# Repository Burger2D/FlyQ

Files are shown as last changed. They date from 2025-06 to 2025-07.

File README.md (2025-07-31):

# FlyQ
An Ultralight fixed-wing autonomous UAV. It is designed to be a flying wing with a single pusher propeller at the back. The airframe is made of XPS foamboard for lightweight-ness.
I plan to eventually fly it with a sidestick.

Why?
It all started with [this video by rctestflight](https://www.youtube.com/watch?v=ULlNktaOUy8), I think. I was fascinated by the idea of a fixed-wing flying objects that and the pictures it captured. I wanted to build something like that, but I wanted it to be ultralight and autonomous. So I started researching on the different types of drones and decided what I want to build. I wanted to start a YSWS with this too (#firefly plug) that is basically this. I am happy I am able to get this far with it.

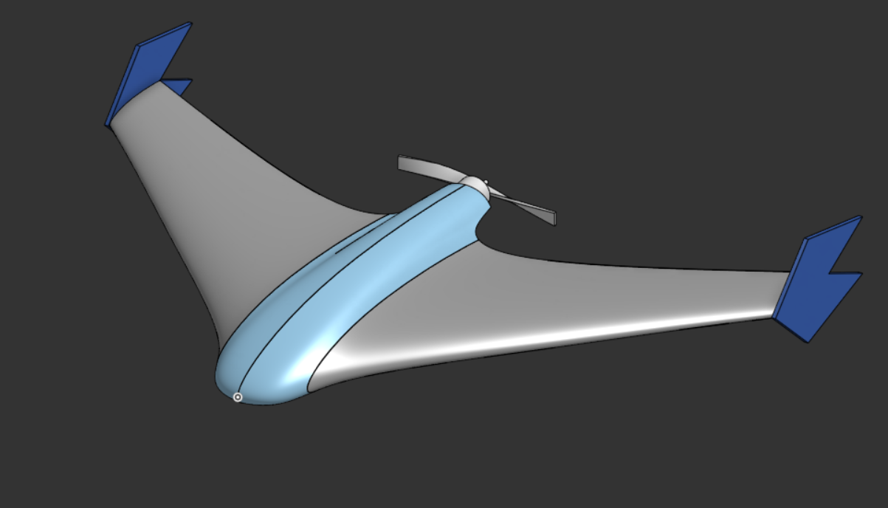
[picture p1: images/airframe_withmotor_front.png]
FlyQ Airframe Design Front

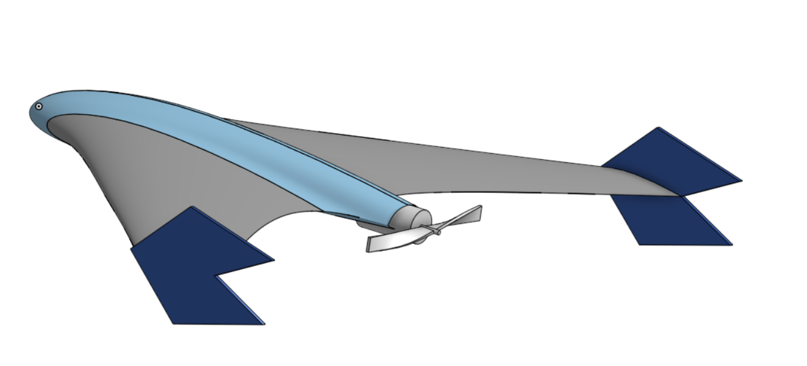
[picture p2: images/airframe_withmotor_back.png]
FlyQ Airframe Design Back

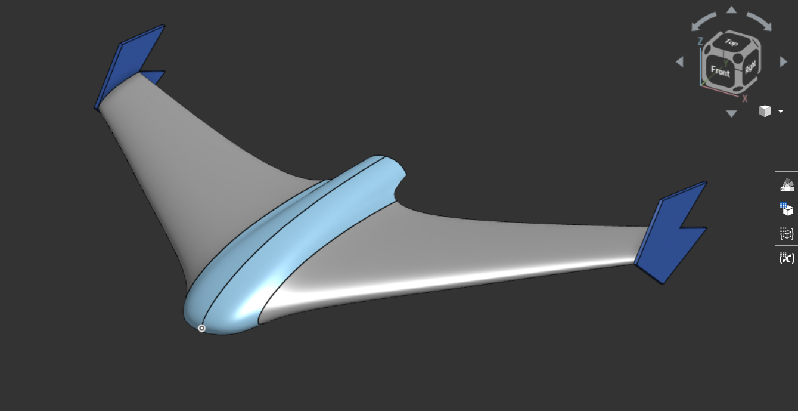
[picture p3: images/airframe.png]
FlyQ Airframe Design CAD


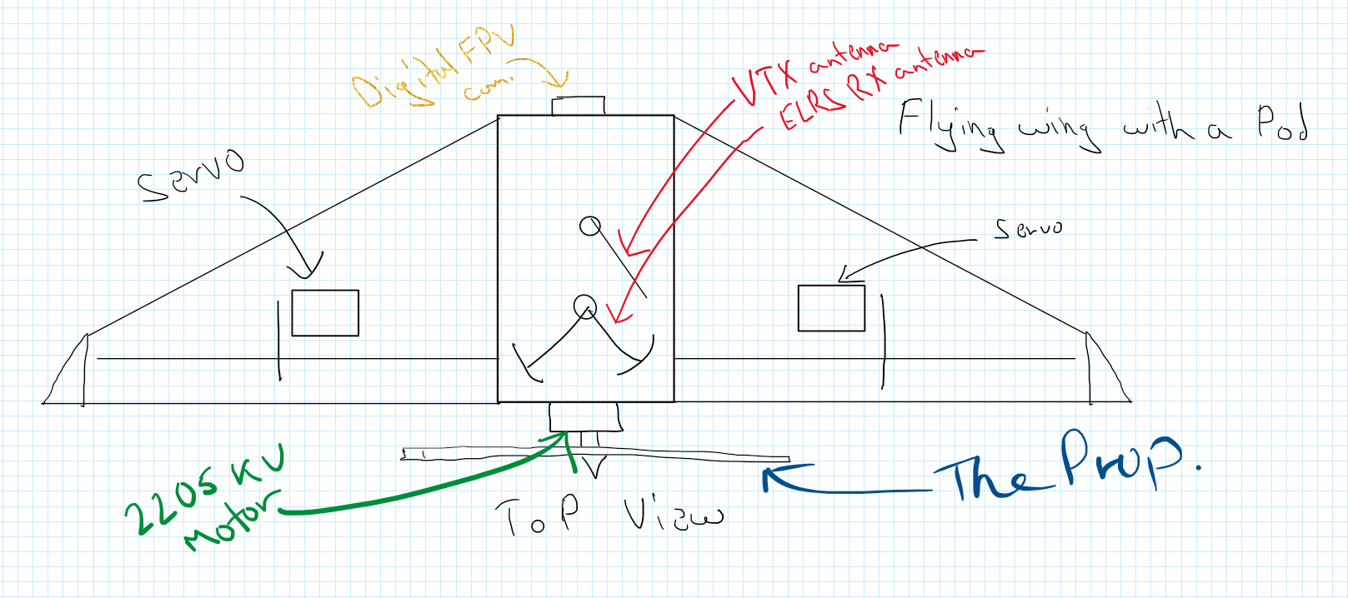
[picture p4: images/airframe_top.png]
FlyQ Airframe Design Top


List:
- [x] Finalise Project Goals
- [x] Finalised Parts List
- [x] Finalised Budget
- [x] Finalised Design
- [x] Tech Work, Arch.

## BOM

| Category | Component Name | Part Number | Quantity | Unit Cost | Total Cost | Supplier | Link |
| --- | --- | --- | --- | --- | --- | --- | --- |
| FC | SpeedyBee F405 WING MINI Fixed Wing Flight Controller | 2008125 | 1 | $38.54 | $38.54 | Speedybee via Banggoods | [https://www.banggood.com/SpeedyBee-F405-WING-MINI-Fixed-Wing-Flight-Controller-Support-INAV-Ardupilot-VTOL-for-RC-Airplane-p-2008125.html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](https://www.banggood.com/SpeedyBee-F405-WING-MINI-Fixed-Wing-Flight-Controller-Support-INAV-Ardupilot-VTOL-for-RC-Airplane-p-2008125.html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) |
| GPS | HGLRC M100 5883 GPS Module M10 Chip with QMC 5883 Compass Ceramic Antenna | 1993147 | 1 | $13.95 | $13.95 | HGLRC via Banggoods | [https://www.banggood.com/HGLRC-M100-5883-GPS-Module-M10-Chip-with-QMC-5883-Compass-Ceramic-Antenna-for-RC-Drone-FPV-Racing-Helicopter-Airplane-p-1993147.html?ID=5222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](https://www.banggood.com/HGLRC-M100-5883-GPS-Module-M10-Chip-with-QMC-5883-Compass-Ceramic-Antenna-for-RC-Drone-FPV-Racing-Helicopter-Airplane-p-1993147.html?ID=5222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) |
| Motor | Readytosky 2205 2300KV 3-4S CW CCW Brushless Motor | 447-M-020 | 2 | $8.66 | $8.66 | Readytosky via Evelta | [https://evelta.com/readytosky-2205-2300kv-3-4s-cw-ccw-brushless-motor/?](https://evelta.com/readytosky-2205-2300kv-3-4s-cw-ccw-brushless-motor/?) |
| ESC | Readytosky 30A 2-4S ESC with 3.5mm Banana Connector | 447-E-064-B21 | 1 | $5.51 | $5.51 | Readytosky via Evelta | [https://evelta.com/readytosky-30a-2-4s-esc-with-3-5mm-banana-connector/](https://evelta.com/readytosky-30a-2-4s-esc-with-3-5mm-banana-connector/) |
| ELRS RX | Radiomaster RP3 ExpressLRS ELRS 2.4GHz LNA+PA Dual Antenna Nano Diversity Receiver | 1978249 | 1 | $19.95 | $19.95 | Radiomaster via Banggoods | [https://www.banggood.com/Radiomaster-RP3-ExpressLRS-ELRS-2_4GHz-LNA+PA-Dual-Antenna-Nano-Diversity-Receiver-for-Whoops-FPV-RC-Racing-Drone-Airplane-p-1978249.html](https://www.banggood.com/Radiomaster-RP3-ExpressLRS-ELRS-2_4GHz-LNA+PA-Dual-Antenna-Nano-Diversity-Receiver-for-Whoops-FPV-RC-Racing-Drone-Airplane-p-1978249.html) |
| Battery Charger | TooklitRC M6D Charger | 2025007 | 1 | $40.00 | $40.00 | TookkitRC via Amazon | [https://www.banggood.com/Eachine-Sphere-Link-5_8GHz-WIFI-Digital-HD-800mW-FPV-Transmitter-VTX-with-1080P-FOV-140-FPV-Camera-MAVLINK-Protocol-Based-on-OpenIPC-for-RC-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](https://www.amazon.in/ToolkitRC-Screen-Multi-Function-Charger-Diagnostics/dp/B07W2X7L6D) |
| Prop | Pro-Range Propellers 6042(6X4.2) Tri Blade Flash 2CW+2CCW 2 Pair Pack- Black | | 1 | $2.97 | $2.97 | Pro-range via Robu.in | [https://robu.in/product/orange-hd-604260x4-2-tri-blade-flash-propellers-2cw2ccw-2-pair-black/](https://robu.in/product/orange-hd-604260x4-2-tri-blade-flash-propellers-2cw2ccw-2-pair-black/) |
| Battery | Samsung INR18650-35E 7.4V 3500mAh 2C 2S1P Li-ion Battery Pack | | 1 | $12.00 | $12.00 | Pro-range via Robu.in | [https://robu.in/product/samsung-inr18650-35e-7-4v-3500mah-2c-2s1p-li-ion-battery-pack/](https://robu.in/product/samsung-inr18650-35e-7-4v-3500mah-2c-2s1p-li-ion-battery-pack/) |
| Drone Airframe | LW-PLA | | 1 | $35 | $35 | Generic via Amazon |  [https://3dzone.in/polymaker-polylite-lw-pla-filament-1-75-0-8kg/?attribute_pa_color=black](https://3dzone.in/polymaker-polylite-lw-pla-filament-1-75-0-8kg/?attribute_pa_color=black) |
| Drone Airframe | Carbon Fiber Spars | | 1 | $3.22 | $3.22 | Generic via Robu.in | [https://robu.in/product/pultruded-carbon-fiber-tube-hollow-3mmod-1-5mm-id-1000mm-pack-of-2](https://robu.in/product/pultruded-carbon-fiber-tube-hollow-3mmod-1-5mm-id-1000mm-pack-of-2) |
| Misc. | Misc. | | | $15.00 | $15.00 | | |
| Price Increases. | Misc. | | | $35.00-40.00 | $35-40.00 | | |
| | Total | | | | ~$250 | | |
> Price Increases in the above table refer to the increase in price due to a sale ending in Banggoods (Hobby days), from where I am sourcing some parts, this is to offset that cost. 
> Misc. refers to other stuff I may need during the build, Plastic Glue, shipping costs to mohid to ship a few things etc. 

Onshape: https://cad.onshape.com/documents/3a31bd101055f48e2c57a97f/w/3223f853520e071ef3d94c1a/e/74b33148177611be13b0c74b

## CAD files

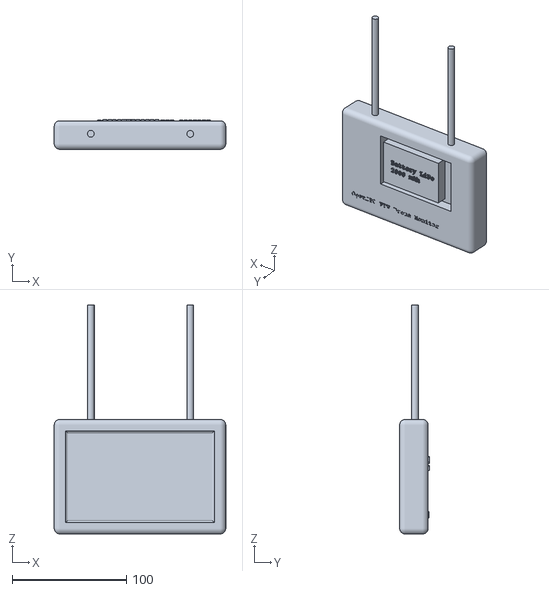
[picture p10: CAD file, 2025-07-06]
FPV_monitor.stl
150.0 x 26.0 x 200.2

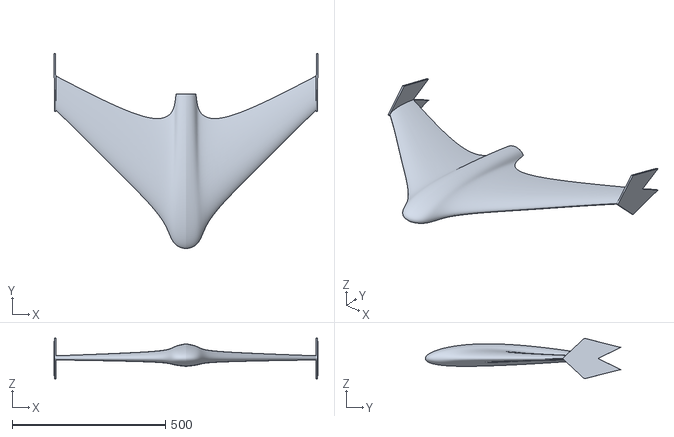
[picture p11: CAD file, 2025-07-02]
airframe_onshape.stl
861.5 x 637.1 x 132.3

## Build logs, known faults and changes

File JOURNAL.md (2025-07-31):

---
title: "FlyQ"
author: "Burger"
description: "Fixed-wing ultralight autonomous UAV"
created_at: "2025-06-01"
total_time: "~50 hours"

---

# FlyQ
An Ultralight fixed wing autonomous UAV.
Note: Not all parts listed from June 1st-6th are used.

## June 1st
Project inception, I researched on the different types of drones and decided what I want to build. Here is all of the research condensed down for reader's consumption.
Project goals:
 - ultralight
 - should have autonomous flying capabilities with failsafe RTH
 - medium range (4-8 km)
 - cameras
 - fixed wing
 - durable
 
Considering all goals, I have decided:
It is going to be a flying wing design with single rotor at the back (pusher).

FlyQ Airframe Design Top

Time spent: ~3-4 hrs (research)

## June 2nd
Agenda: Airframe
I am researching on the airframe, how it's going to be made, design desisions, extra provisions etc.
I have decided it is best to buy a commercial frame for it being made out of molded EPP foam goes a long way towards crash resistance (EPP foam compresses and does not break (shatter) like defron sheets if I were to DIY it). There are a few downsides to this, notablily this kinda makes future customization on the drone itself a bit difficult but I think that is acctable considering the other factors.
Time spent: ~2-3 hrs
I had some more time today so I have decided to look into which commercial frame that is readyly available here that can be bought.
I am going for a single prop design as it is cheaper due to only one motor being persent and the cruise current being lower for the same reason.
I've chosen the 'Reptile S800 V2 Flying Wing'

I chose this due to it's avaibility in an Indian store and alignment with the project goals. It's made with EPP ensuring the drone dosen't break on impact.
Time spent: ~3 hrs

## June 3rd
Agenda: Flight Control systems
I'll try to decide which control systems to put on drone as per my budget and other factors like compatibility with Ardupilot/INAV (autonomy), ELRS etc.
I've decided to go with the "SpeedyBee F405 WING MINI Fixed Wing Flight Controller"


It is very light at 23g and supports INAV and Ardupilot. It is well within budget at US$35.99 (around $47 USD in Indian sites)
I've checked out some 40 FCs but this seems to be the best in it's capabilities and price based on the STM32F405. It has integrated IMU, barometer and OSD.

I've read the INAV and Ardupilot docs to compare which one would be simpler for my use case. As I see, Ardupilot is a much more sophisticated solution for drone piloting, while [INAV](https://github.com/iNavFlight/inav) is simpler, and fits my usecase better, which is autonomy for some time, not very long range ops.

In my search for a good FC, I initially came across Matek F405-Wing, which is a nice FC and what I was going to use until I continued searching and found the SpeedyBee F405 Wing Mini, which is much lighter than the Matek version. I also came across the Matek F722-Wing, it is also a nice FC, a little too nice, it's too expensive for this lightweight platform. Betaflight FCs (F411s etc) were too slow to support everything and that kinda raised some questions about it's stabilty running everything.
This FC was a stack option containing PDBs and current sensors inbuilt. Also has Barometers for altitude measurement. 
My search for the FC was narrowed down with the help of INAV docs with which I could tell if it had the minimum requirements for my needs, as it needed to run INAV. (ref feature 1 [here](https://github.com/iNavFlight/inav?tab=readme-ov-file#features))
Read some more about flying with INAV here [https://github.com/iNavFlight/inav/blob/master/docs/INAV_Fixed_Wing_Setup_Guide.pdf](https://github.com/iNavFlight/inav/blob/master/docs/INAV_Fixed_Wing_Setup_Guide.pdf) and [https://github.com/iNavFlight/inav/blob/master/docs/Navigation.md](https://github.com/iNavFlight/inav/blob/master/docs/Navigation.md)

Also selected the GPS module to be used with this FC, it's a Flywoo GOKU GM10 Mini V3 GPS

Time spent: ~4 hrs

## June 4th
Agenda: Other parts
Selecting other parts in accordance with compatibilty with FC, budget and project goals.
### Motor
XING 2205 FPV Motor (12/M2) - 2300KV

Within budget, efficient rating.
This is a popular FPV motor within FPV circles. At 2300KV, it produces enough thrust to cruise comfortably with just the right amount of energy. It's reliable, lightweight and efficient, ideal for this project.
### ESC
Readytosky 40A 2-6S Multi-Rotor UAV Drone ESC
Readytosky 40A 2-6S Multi-Rotor UAV Drone ESC, Brushless Electronic Speed Controller for F450, X500, S500, ZD550 RC Helicopters and Quadcopters, OPTO Design, Lightweight 33.2g.
Also, within budget and has a sufficient rating.
At 40A, this is more than enough for what the motor will ever experience, with enough headroom for boosts past the normal every once in a while. It is reasonably priced and well-known.
### ELRS RX

MATEKSYS ELRS 2.4GHz Vario Receiver ELRS-R24-V
This is an important component (although one could say this for all of them). It's an [ELRS](https://www.expresslrs.org/) receiver, which stands for [Express Long Range System](https://www.expresslrs.org/), is a "High Performance Open Source Radio Control Link" optimised for long range and low latency. Read a lot in the [ELRS docs](https://www.expresslrs.org/software/mavlink/). It can pull some long-range (50+ km) stuff even on 2.4 GHz.

### Camera DVR

It is a RunCam Mini FPV DVR, fits right in the budget. 
It was meh, i didn't quite like it as it can't record in HD but I guess for that price it's the best I can get.

### Camera
Buy Caddx Ant Lite Analog Camera at Best Price
It's a Caddx Ant Lite Analog Camera (FPV Cycle Edition) (4:3), cheapest while having great quality.
Its cheap, at this price point it's hard to beat. Great for this build.
This is cool, cheap and probably not the camera for drones so would need to hack it for it to work with the FC and VTx.

Spent a lot of time reading the ELRS and INAV docs. Also got help from the Oscar Liang blog. Spent some time researching batteries.

Time spent: ~6-8 hrs

## June 5th
Remaining electronic stuff for the drone.

### VTX
 SpeedyBee TX800 5.8 GHz VTX
 One of the few available VTxs here, it's cheap-er than most and the transmit power is under limits and enough for mid range stuff.
### Battery

 Samsung INR18650-35E 7.4V 3500mAh 2C 2S1P Li-ion Battery Pack
 Nice value for the battery pack, it's good that it's made by robu and sold by robu.
### VTX Antenna
Buy Pagoda 2 Antenna 5.8GHz with cover Online at Best Price in India
Pagoda 2 Antenna 5.8GHz with cover
Good antenna, cheap, would be used for the drone VTx.

Time spent: ~4-5 hrs

## June 6th
Ground station stuff

### VRX
5.8G UVC OTG Android AV Phone Receiver
5.8G UVC OTG Android AV Phone Receiver

> ## Budget check (retail prices at 1USD = 85.76INR)
>  Airframe - $49.05
>  FC - $39.77
>  GPS - $19.80
>  Motor - $9.32
>  ESC (!!) - $8.71
>  ELRS RX - $29.71
>  DVR - $17.99
>  Camera - $18.80
>  VTX - $28 USD 
>  Battery - $12.57
>  Antenna (drone) - $4.19
>  ### Total till now - $ 246.94
Prices taken from the best retailers found. That took too long. Finding the cheapest non-scammy retailer for niche stuff is a bit hard. More so in India, thankfully, I was able to find retailers for all the parts. 

Ah, Houston, we have a problem.
That price is too high; it's more than I thought for just this part of the project. I must do something about it. I suppose I'd have to allow myself to import and change parts for better, more cost-effective alternatives. 

Did some research on drone parts from YouTube and Oscar Liang's blog. They are a nice resource on builds like these, not just these but most other builds would benifit from the infomative blogs and youtube reviews.
Time spent: 4.5 hrs

## Break
I took a break. Returned on June 15th

We can do better. Revamping materials and stategry to bring this greatly under budget.
### To do so, we're changing the following:
- Allowing imports
- Frame
- FC
- Camera and VTX

I lost of count of time spent on doing this, I have been at it for 2+ days at this point.

But I have selected all the new parts.

> I've listed the new parts below, the cateories that aren't listed have kept their initial selection.
> GPS - HGLRC M100 5883 GPS Module M10 Chip with QMC 5883 Compass Ceramic Antenna - $14.39
> Motor - Readytosky 2205 2300KV 3-4S CW CCW Brushless Motor -  $8.69
> ESC - Generic ESC 30A - $4
> ELRS RX - Radiomaster RP3 ExpressLRS ELRS 2.4GHz LNA+PA Dual Antenna Nano Diversity Receiver for Whoops FPV RC Racing Drone Airplane - $21.73
> FPV setup, full (VTX, VRX, Camera, Antenna Combo) - Eachine Sphere Link 5.8GHz WIFI Digital HD 800mW - $67.35
> Servo - TowerPro SG90 9G Mini - $4

This brings the drone hardware cost below $170 (from ~$250)

Below is the design for the drone airframe, it's going to be built out of XPS foam boards, supported by carbon fiber spars and reinforced with packing tape.

FlyQ Airframe Design Top
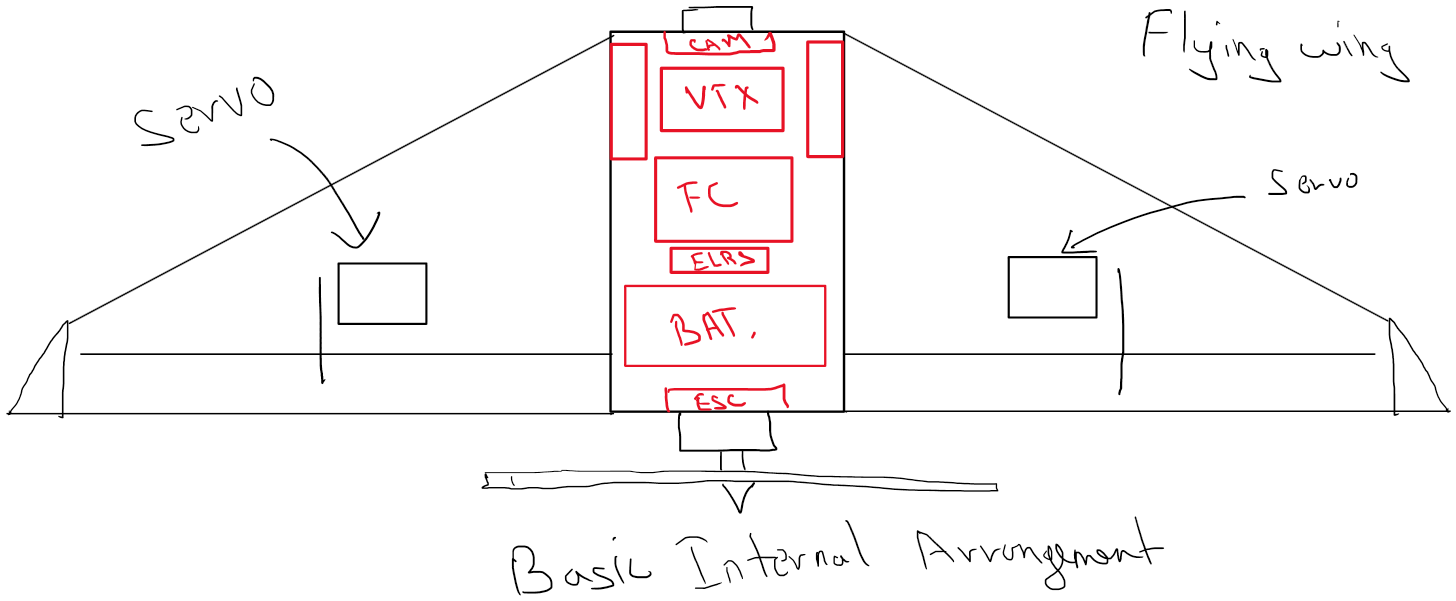
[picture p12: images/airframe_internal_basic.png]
FlyQ Airframe Design Inside (basic)


For Accurate wiring, I'd need to have the hardware in hand, so I will not be able to do that until the parts arrive.

For firmware, I'd be using INAV 6.0 for autonomy and Rocketmaster Pocket for ELRS control link, and using it will passthrough telementry data to the ground station.

I am also designing a custom PCB DVR for the drone, it will be used to record the video feed from the camera on the drone onto a SD card onboard for even higher image quality and data recovery.

For FPV setup, I will be using the Eachine Sphere Link 5.8GHz WIFI Digital HD 800mW, which is a combo of VTX, VRX, Camera and Antenna. It is a digital setup and will provide much better image quality than analog setups, at a cost that is cheaper than most.

For the FPV ground viewing, I'd be using a phone initially with plans to bind it with a rpi02w soon.

I have carefully selected all the parts to ensure they are compatible with each other and fit within the budget. I have also taken into account the weight of each component to ensure the drone remains ultralight.

XPS foam boards are great for this project as they are lightweight and help me keep the drone within limits.

This concludes Part 1 of the FlyQ project.

spent ~15 days designing, refining and finalizing the design, parts and budget.

## 27th June
wait a second, wasn't that the end?
apparently not, there's more to come.

Designed with a meticulous selection of components to achieve a compact, efficient, and high-performance system.

I present you FlyQ, the ultralight fixed-wing autonomous UAV.

FlyQ Airframe Design Top
.stl files in root

# Summery:

Bit of a rewrite, but this improves the formatting of the initial part (sourcing parts [new ones])

Let us recap the project goals
Project goals:
 - ultralight
 - should have autonomous flying capabilities with failsafe RTH
 - medium range (4-8 km)
 - cameras
 - fixed wing
 - durable

|Sr. No.|Image |Name |Category |Sub-Category|Main Use |Considerations while choosing |Cost  |Extra remarks |
|---|---|---|---|---|---|---|---|---|
|1 |https://cdn11.bigcommerce.com/s-fhxxhuiq8q/images/stencil/500x500/products/240/1367/SB_WING-MINI-1__04828.1707096339.jpg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|SpeedyBee F405 WING MINI Fixed Wing Flight Controller |Electronics|Main control|Flight Controller|Cheap, Very light, Support INAV/Ardupilot, built in barometer, current sensor, OSD and UART capabilities, ecosystem. Entire stack|$39.00|Will probably buy from Banggoods as while it's $2 cheaper when directly compared, the shipping cost takes ~$15.|
|2 |https://m.media-amazon.com/images/I/51ASMWWGR7L._UF1000,1000_QL80_.jpg |HGLRC M100 5883 GPS Module M10 Chip with QMC 5883 Compass Ceramic Antenna |Electronics|Main control|GPS |Cheap, Has Compass, Accuracy, Latest M10 chip, Has a compass, Lightweight |$13.00| |
|3 |https://m.media-amazon.com/images/I/41W5V3w09pL._UF350,350_QL80_.jpg |Readytosky 2205 2300KV 3-4S CW CCW Brushless Motor |Electronics|Main control|Motor |Well known FPV motor, reletively lightweight |$8.69 |India shop |
|4 |https://ae01.alicdn.com/kf/Sd7f9c6000a61405a96563ed8aa87b3907.jpg_960x960.jpg |Readytosky 40A 2-4S ESC with 3.5mm Banana Connector |Electronics|Power |ESC |Well known FPV ESC, within limits, reletively lightweight and cheap |$6.14 |would have bought the 30A 2-4S varient for a dollar less if it was in stock; Have to solder connections |
|5 |https://ueeshop.ly200-cdn.com/u_file/UPAX/UPAX406/2308/23/photo/RP3-V2-Detail-Page-EN-Mobile01-9e6f.jpg |Radiomaster RP3 ExpressLRS ELRS 2.4GHz LNA+PA Dual Antenna Nano Diversity Receiver|Electronics|RF |ELRS RX |Best range vs. Cost, Reletively cheap |$20.00|Have to solder connections |
|6 |https://imgaz3.staticbg.com/thumb/large/oaupload/banggood/images/78/EF/4299da5d-869b-45a3-80de-5bc60856469b.jpg.webp |Eachine Sphere Link 5.8GHz WIFI Digital HD |Electronics|Accessory |FPV system |Unbeatable price for a HD FPV system (Camera + VTX + Reciever) |$70.00| |
|7 |https://encrypted-tbn0.gstatic.com/images?q=tbn:ANd9GcSmdgw4eVREMJC2hH6P0phcIXBU7NcqDeXbFA&s |Pro-Range Propellers 6042(6X4.2) Tri Blade Flash 2CW+2CCW 2 Pair Pack- Black |Structural |Thrust |Prop. |Cheap, within parameters. Aerodynamic efficiency |$3.00 | |
|8 |https://encrypted-tbn0.gstatic.com/images?q=tbn:ANd9GcRjw1WUnR5fEDjanitMtx7iaRLjqHcGkv8usQ&s |Samsung INR18650-35E 7.4V 3500mAh 2C 2S1P Li-ion Battery Pack |Electronics|Power |Battery |Cheap, Good Wh vs. Price |$12.00| |

Here's an accounting sheet for the project, it contains all the parts I have ordered in relation to it, by all, I actually mean all, even the itty bitty ones.
You can check it out [here](https://docs.google.com/spreadsheets/d/1skVhD2z50aWqVVDrjqqTZmjcNkN75A2qXTNfnrAGnOc/edit?usp=sharing).

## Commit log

2025-06-20 ready for submission
    [BOM.csv]
2025-07-02 add stl files
    [BOM.csv, Part Studio_1_onshape.stl]
2025-07-02 add design files and updates
    [BOM.csv, Part Studio_1_onshape.stl]
2025-07-07 better stl file name
    [airframe_onshape.stl]
